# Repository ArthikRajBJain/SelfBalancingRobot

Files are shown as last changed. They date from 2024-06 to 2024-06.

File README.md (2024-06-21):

# Self Balancing Robot

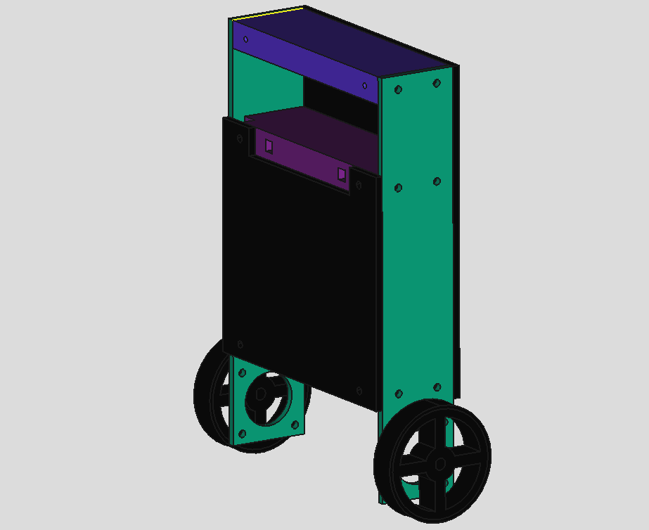
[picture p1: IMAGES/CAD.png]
Watch the video (https://drive.google.com/file/d/1cC-Chdwye79UuMQegcqwbnqvilcww2Fp/view?usp=drive_link)


This is the project involving the development of a Self Balancing Robot. It uses the Proportional, Integraal and Derivative(PID) control algorithm to balance itself. It uses the 6 Degrees of Freedom(DOF) Inertial Measurement Unit(IMU) as the sensor to get the angle data.

<br>
**Process Variable:**  Angle(Roll) (deg)
<br>
**Control Variable:**  Speed of the Motors (mm/sec)
<br>
**Setpoint        :**  0 deg (calibrated for upright position)

<br>

The motors used are the stepper motors hence the relationship between the number of steps and speed is non-linear in nature, hence PID algorithm can not be used unless the linearization is performed.

<br>
$Speed = {157 \over 6400*(40+20n)*10^(-6)}$
Here the speed is calculated in mm/sec, and **n** is the number of steps.
<br>
$n = {(157*10^(6) /over 5400*Speed*20) - (40 /over 20)}$
<br>

To mitigate the problem of nonlinear-system, the PID algoritm is implemented on **Speed** rather than the number of steps **n**.

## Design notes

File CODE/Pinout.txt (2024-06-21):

MotorP
12 - INA
14 - STP
27 - DIR

MotorN
33 - INA
25 - STP
26 - DIR

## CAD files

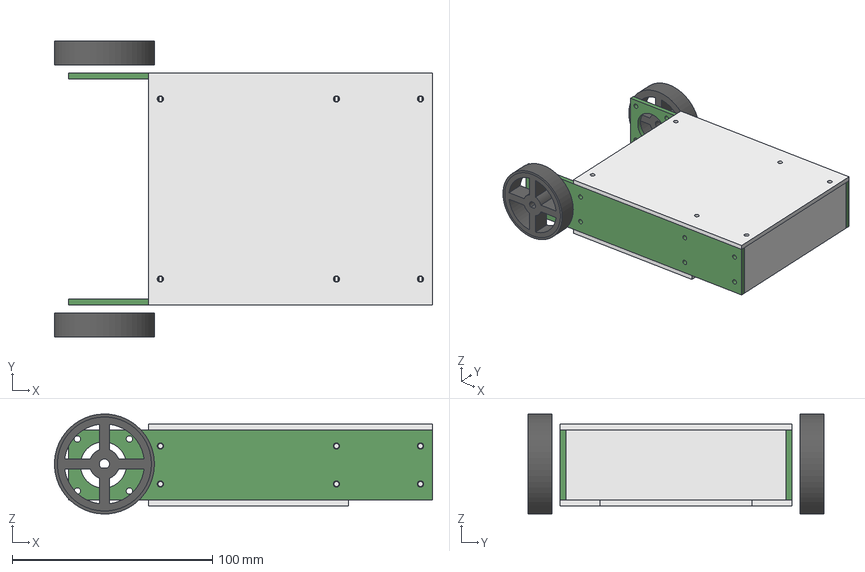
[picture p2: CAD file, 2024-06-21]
CAD/SelfBalancing/SelfBalancing.FCStd
189.0 x 148.0 x 50.0 mm
WheelBody
WheelRubberBody
SideBody
SeparatorBodyTop
SeparatorBodySecond
SeparatorBodyThird
FrontPanelBody
BackPanelBody
WheelBody001
SideBody001
WheelRubberBody001

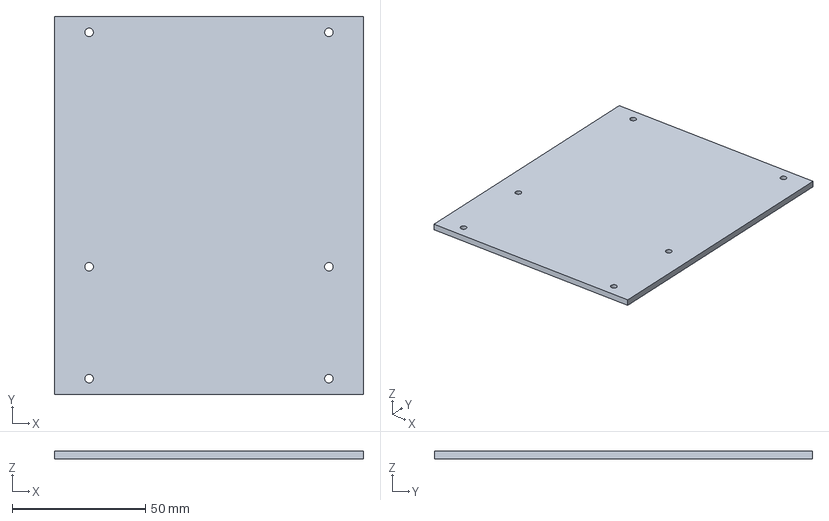
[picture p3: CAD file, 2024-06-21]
CAD/SLICE/SelfBalancing-BackPanelBody.3mf
116.0 x 142.0 x 3.00 mm

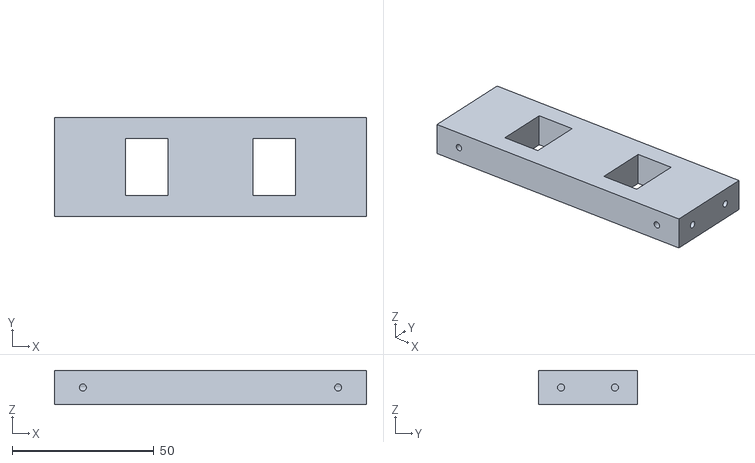
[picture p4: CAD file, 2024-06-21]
CAD/STL/SelfBalancing-SeparatorBodyThird.stl
110.0 x 35.0 x 12.0

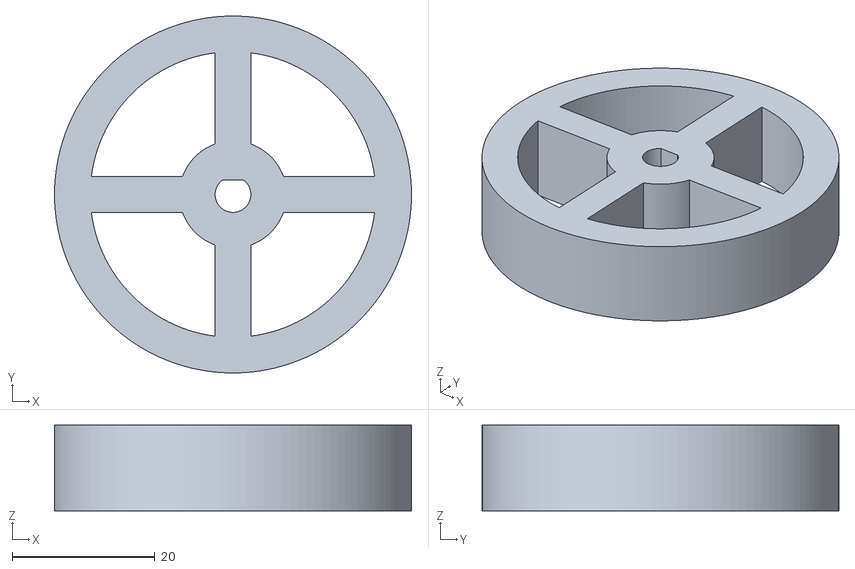
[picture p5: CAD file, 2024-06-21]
CAD/STL/SelfBalancing-WheelBody.stl
50.0 x 50.0 x 12.0

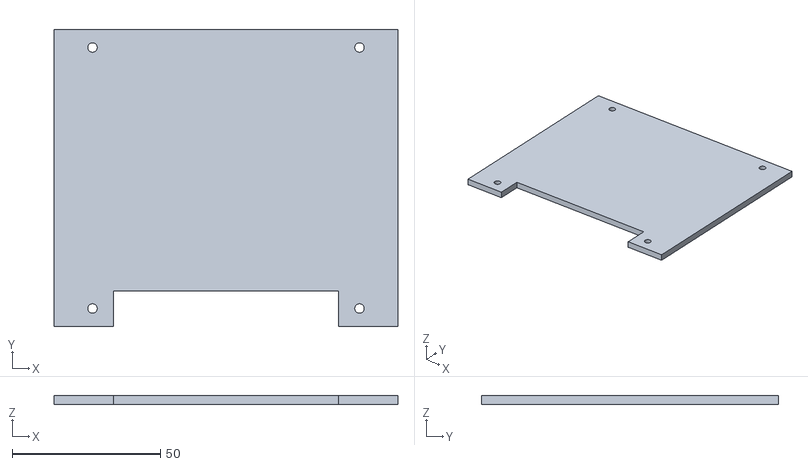
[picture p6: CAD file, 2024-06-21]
CAD/STL/SelfBalancing-FrontPanelBody.stl
116.0 x 100.0 x 3.00

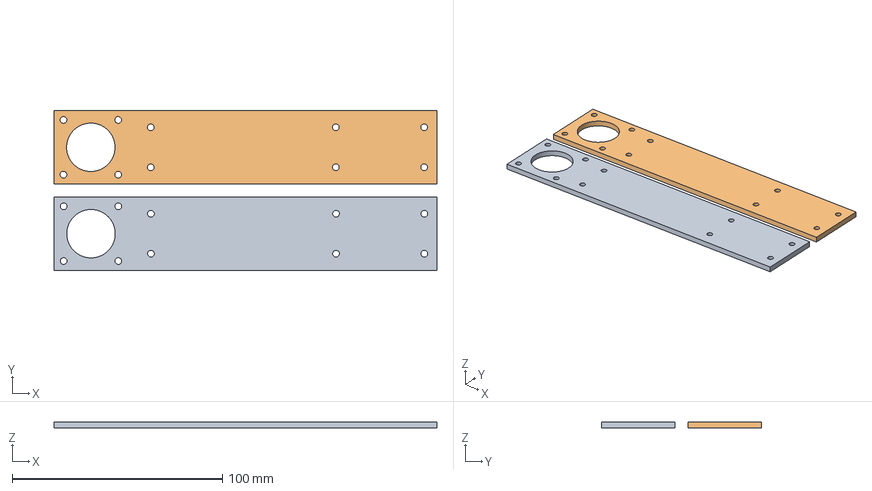
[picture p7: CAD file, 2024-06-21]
CAD/SLICE/SelfBalancing-SideBody.3mf
182.1 x 76.1 x 3.00 mm
SelfBalancing-SideBody.stl x 2

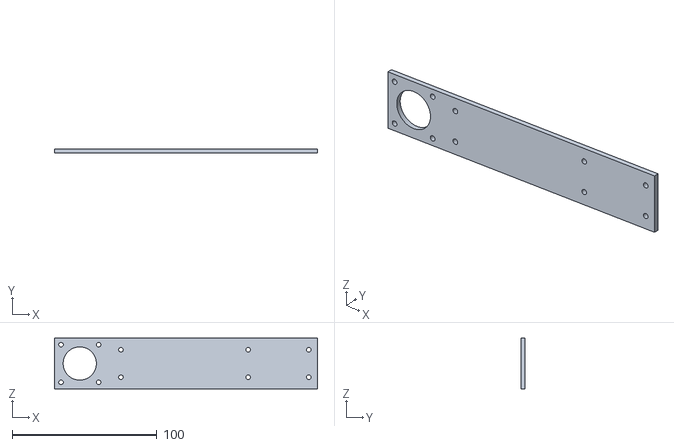
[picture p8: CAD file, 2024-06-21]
CAD/STL/SelfBalancing-SideBody.stl
182.0 x 3.00 x 35.0

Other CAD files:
CAD/SLICE/SelfBalancing-SeparatorBodyTop.3mf
CAD/SLICE/SelfBalancing-SeparatorBodyThird.3mf
CAD/STL/SelfBalancing-SeparatorBodyTop.stl
CAD/SLICE/SelfBalancing-WheelBody.3mf
CAD/STL/SelfBalancing-SeparatorBodySecond.stl
CAD/SLICE/SelfBalancing-FrontPanelBody.3mf
CAD/STL/SelfBalancing-BackPanelBody.stl
CAD/SLICE/SelfBalancing-SeparatorBodySecond.3mf

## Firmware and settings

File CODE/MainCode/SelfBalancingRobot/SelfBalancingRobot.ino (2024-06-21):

#include <WiFi.h>
#include <ESPmDNS.h>
#include <NetworkUdp.h>
#include <ArduinoOTA.h>
#include "BluetoothSerial.h"
#include "Wire.h"
#include "PID.h"
#include "math.h"

const char *ssid = "XXXXXXX";
const char *password = "XXXXXXX";

String device_name = "SelfBalancingRobot";
hw_timer_t *timer = NULL;
double ltime = 0;
double LSpeed = 0, RSpeed = 0, LMotor = 0, RMotor = 0, LMotorCount = 0, RMotorCount = 0;
bool LDirection = 0, RDirection = 0;
bool LITRFlag = 0, RITRFlag = 0;
double input, output, setpoint = 0, Kp = 50, Ki = 0.005, Kd = 0.0001, setpointMem = 0;
bool direction = 0;
int16_t rax, ray, raz, rgx;
double ax, ay, az, axcal, aycal, azcal;
double aroll, groll, grollcal, arollcal;
double froll;

PID pid(&input, &output, &setpoint, Kp, Ki, Kd, direction, micros());

void IRAM_ATTR onTimer() {
  LMotorCount++;
  if (LITRFlag == 1) {
    digitalWrite(25, LOW);
    LITRFlag = 0;
    LMotorCount = 0;
  }
  if (LMotorCount > LMotor) {
    digitalWrite(25, HIGH);
    LITRFlag = 1;
  }

  RMotorCount++;
  if (RITRFlag == 1) {
    digitalWrite(14, LOW);
    RITRFlag = 0;
    RMotorCount = 0;
  }
  if (RMotorCount > RMotor) {
    digitalWrite(14, HIGH);
    RITRFlag = 1;
  }
}

BluetoothSerial SerialBT;

int numFinder(double speed) {
  return int(round((1218.75 / speed) - 2.0));
}

TaskHandle_t task_loop1;
void esploop1(void *pvParameters) {
  setup1();

  for (;;) {
    loop1();
  }
}

void setup() {
  // Motor N
  pinMode(33, OUTPUT);  //INA
  pinMode(25, OUTPUT);  //STP
  pinMode(26, OUTPUT);  //DIR
  // Motor P
  pinMode(12, OUTPUT);  //INA
  pinMode(14, OUTPUT);  //STP
  pinMode(27, OUTPUT);  //DIR
  digitalWrite(33, HIGH);
  digitalWrite(12, HIGH);
  digitalWrite(26, LOW);
  digitalWrite(27, HIGH);
  timer = timerBegin(1000000);
  timerAttachInterrupt(timer, &onTimer);
  timerAlarm(timer, 20, true, 0);
  xTaskCreatePinnedToCore(
    esploop1,               /* Task function. */
    "loop1",                /* name of task. */
    10000,                  /* Stack size of task */
    NULL,                   /* parameter of the task */
    1,                      /* priority of the task */
    &task_loop1,            /* Task handle to keep track of created task */
    !ARDUINO_RUNNING_CORE); /* pin task to core @ */
  Serial.begin(115200);
  ltime = micros() + 4000;
  pid.setOutputLimits(-613, 613);
  pid.updateTime(micros());
  Wire.begin();
  Wire.setClock(400000);
  Serial.begin(115200);
  //POWER MANAGEMENT
  Wire.beginTransmission(0x68);
  Wire.write(0x6B);
  Wire.write(0x00);
  Wire.endTransmission();
  //GYROSCOPE RANGE(+/-250dps)
  Wire.beginTransmission(0x68);
  Wire.write(0x1B);
  Wire.write(0x00);
  Wire.endTransmission();
  //ACCELEROMETER RANGE(+/-4g)
  Wire.beginTransmission(0x68);
  Wire.write(0x1C);
  Wire.write(0x08);
  Wire.endTransmission();
  //FILTERING
  Wire.beginTransmission(0x68);
  Wire.write(0x1A);
  Wire.write(0x03);
  
  Wire.endTransmission();
  ltime = micros();
  for(int i=0;i<500;i++)
  {
    Wire.beginTransmission(0x68);
    Wire.write(0x43);
    Wire.endTransmission();
    Wire.requestFrom(0x68, 2);
    rgx = rgx + Wire.read()<<8|Wire.read();
    while (ltime > micros());
    ltime = micros() + 4000;
  }
  rgx = rgx/500.0;
  grollcal = -rgx*0.000031;
  Wire.beginTransmission(0x68);
  Wire.write(0x3B);
  Wire.endTransmission();
  Wire.requestFrom(0x68, 6);
  rax = Wire.read()<<8|Wire.read();
  ray = Wire.read()<<8|Wire.read();
  raz = Wire.read()<<8|Wire.read();
  ax = rax/8200.0;
  ay = ray/8200.0;
  az = raz/8200.0;
  // arollcal = atan(ax/(sqrt(ay*ay + az*az)))*-57.3;
  arollcal = atan(ay/(sqrt(ax*ax + az*az)))*62.1325;
  pinMode(33, OUTPUT);  //INA
  pinMode(25, OUTPUT);  //STP
  pinMode(26, OUTPUT);  //DIR
  // Motor P
  pinMode(12, OUTPUT);  //INA
  pinMode(14, OUTPUT);  //STP
  pinMode(27, OUTPUT);  //DIR
  digitalWrite(33, LOW);
  digitalWrite(12, LOW);
  digitalWrite(26, LOW);
  digitalWrite(27, HIGH);
  pid.setDeadzone(-5, 5);
}

int number;

void loop() {
  Wire.beginTransmission(0x68);
  Wire.write(0x3B);
  Wire.endTransmission();
  Wire.requestFrom(0x68, 6);
  rax = Wire.read()<<8|Wire.read();
  ray = Wire.read()<<8|Wire.read();
  raz = Wire.read()<<8|Wire.read();
  ax = rax/8192.0;
  ay = ray/8192.0;
  az = raz/8192.0;
  if(az >= 0) aroll = -(arollcal - atan(ay/(sqrt(ax*ax + az*az)))*62.1325);
  else aroll = (arollcal - atan(ay/(sqrt(ax*ax + az*az)))*62.1325);
  Wire.beginTransmission(0x68);
  Wire.write(0x43);
  Wire.endTransmission();
  Wire.requestFrom(0x68, 2);
  rgx = Wire.read()<<8|Wire.read();
  groll = froll + grollcal + rgx*0.000031;
  froll = groll*0.997 + aroll*0.003;

  input = froll;
  pid.compute(micros());
  if((setpointMem == setpoint) && (output != 0))
  {
    if(output > 0)
    {
      setpoint += 0.007;
      setpointMem = setpoint;
    }
    else
    {
      setpoint -= 0.007;
      setpointMem = setpoint;
    }
  }
  if (output >= 0) {
    digitalWrite(26, LOW);
    digitalWrite(27, HIGH);
    number = numFinder(output);
    LMotor = number;
    RMotor = number;
  } else {
    digitalWrite(26, HIGH);
    digitalWrite(27, LOW);
    number = numFinder(-1 * output);
    LMotor = number;
    RMotor = number;
  }

  if(input >  15 || input < -15)
  {
    digitalWrite(33, HIGH);
    digitalWrite(12, HIGH);
  }

  while (ltime > micros());
  ltime = micros() + 4000;
}

void setup1() {
  WiFi.mode(WIFI_STA);
  WiFi.begin(ssid, password);
  SerialBT.begin(device_name);
  while (WiFi.waitForConnectResult() != WL_CONNECTED) {
    SerialBT.println("Connection Failed! Rebooting...");
    delay(5000);
    ESP.restart();
  }
  ArduinoOTA.setHostname("SelfBalancingRobot");
  ArduinoOTA.setPasswordHash("ee338d1db6a6ed2564dc623d8f11bf8b");
  ArduinoOTA
    .onStart([]() {
      String type;
      if (ArduinoOTA.getCommand() == U_FLASH) {
        type = "sketch";
      } else {  // U_SPIFFS
        type = "filesystem";
      }
      SerialBT.println("Start updating " + type);
    })
    .onEnd([]() {
      SerialBT.println("\nEnd");
    })
    .onProgress([](unsigned int progress, unsigned int total) {
      SerialBT.printf("Progress: %u%%\r", (progress / (total / 100)));
    })
    .onError([](ota_error_t error) {
      SerialBT.printf("Error[%u]: ", error);
      if (error == OTA_AUTH_ERROR) {
        SerialBT.println("Auth Failed");
      } else if (error == OTA_BEGIN_ERROR) {
        SerialBT.println("Begin Failed");
      } else if (error == OTA_CONNECT_ERROR) {
        SerialBT.println("Connect Failed");
      } else if (error == OTA_RECEIVE_ERROR) {
        SerialBT.println("Receive Failed");
      } else if (error == OTA_END_ERROR) {
        SerialBT.println("End Failed");
      }
    });
  ArduinoOTA.begin();
}

char byt;
double KpBT = 0, KiBT = 0, KdBT = 0;
String val;
double remoteTime = 0;

void loop1() {
  ArduinoOTA.handle();
  if(SerialBT.available()) {
    byt = SerialBT.read();
    if(byt == 'P') {
      val = SerialBT.readStringUntil(' ');
      KpBT = val.toDouble();
    }
    if(byt == 'I') {
      val = SerialBT.readStringUntil(' ');
      KiBT = val.toDouble();
    }
    if(byt == 'D') {
      val = SerialBT.readStringUntil('\n');
      KdBT = val.toDouble();
      pid.setTunings(KpBT, KiBT, KdBT);
      SerialBT.print(KpBT);
      SerialBT.print(" ");
      SerialBT.print(KiBT);
      SerialBT.print(" ");
      SerialBT.println(KdBT);
    }
    if(byt == 'F')
    {
      setpoint += 0.7;
    }
    if(byt == 'B')
    {
      setpoint += -0.7;
    }
    if(byt == 'S')
    {
      setpoint = setpointMem;
    }
  }
  SerialBT.print(input);
  SerialBT.print(" ");
  SerialBT.print(setpoint);
  SerialBT.print(" ");
  SerialBT.println(output);
  // Serial.print(input);
  // Serial.print(" ");
  // Serial.print(setpoint);
  // Serial.print(" ");
  // Serial.println(output);
  vTaskDelay(1);
}

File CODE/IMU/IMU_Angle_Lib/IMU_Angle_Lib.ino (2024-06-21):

#include "Wire.h"


int16_t rax, ray, raz, rgx, rgy, rgz;
double ax, ay, az, axcal, aycal, azcal;
double vector;
double ayaw, apitch, aroll, gyaw, gpitch, groll, gyawcal, gpitchcal, grollcal, ayawcal, apitchcal, arollcal;
double fyaw, fpitch, froll;
double ltime;

void setup() 
{
  Wire.begin();
  Wire.setClock(400000);
  Serial.begin(115200);
  //POWER MANAGEMENT
  Wire.beginTransmission(0x68);
  Wire.write(0x6B);
  Wire.write(0x00);
  Wire.endTransmission();
  //GYROSCOPE RANGE(+/-250dps)
  Wire.beginTransmission(0x68);
  Wire.write(0x1B);
  Wire.write(0x00);
  Wire.endTransmission();
  //ACCELEROMETER RANGE(+/-4g)
  Wire.beginTransmission(0x68);
  Wire.write(0x1C);
  Wire.write(0x08);
  Wire.endTransmission();
  //FILTERING
  Wire.beginTransmission(0x68);
  Wire.write(0x1A);
  Wire.write(0x03);
  Wire.endTransmission();
  ltime = micros();
  for(int i=0;i<500;i++)
  {
    Wire.beginTransmission(0x68);
    Wire.write(0x43);
    Wire.endTransmission();
    Wire.requestFrom(0x68, 6);
    rgx = rgx + Wire.read()<<8|Wire.read();
    rgy = rgy + Wire.read()<<8|Wire.read();
    rgz = rgz + Wire.read()<<8|Wire.read();
    while (ltime > micros());
    ltime = micros() + 4000;
  }
  rgx = rgx/500.0;
  rgy = rgy/500.0;
  rgz = rgz/500.0;
  grollcal = -rgx*0.000031;
  gpitchcal = -rgy*0.000031;
  gyawcal = -rgz*0.000031;
  Wire.beginTransmission(0x68);
  Wire.write(0x3B);
  Wire.endTransmission();
  Wire.requestFrom(0x68, 6);
  rax = Wire.read()<<8|Wire.read();
  ray = Wire.read()<<8|Wire.read();
  raz = Wire.read()<<8|Wire.read();
  ax = rax/8200.0;
  ay = ray/8200.0;
  az = raz/8200.0;
  apitchcal = atan(ay/(sqrt(ax*ax + az*az)))*-57.3;
  arollcal = atan(ax/(sqrt(ay*ay + az*az)))*-57.3;
}

double start;

void loop() 
{
  start = micros();
  Wire.beginTransmission(0x68);
  Wire.write(0x3B);
  Wire.endTransmission();
  Wire.requestFrom(0x68, 6);
  rax = Wire.read()<<8|Wire.read();
  ray = Wire.read()<<8|Wire.read();
  raz = Wire.read()<<8|Wire.read();
  ax = rax/8200.0;
  ay = ray/8200.0;
  az = raz/8200.0;
  apitch = apitchcal + atan(ay/(sqrt(ax*ax + az*az)))*57.3;
  aroll = arollcal + atan(ax/(sqrt(ay*ay + az*az)))*57.3;
  Wire.beginTransmission(0x68);
  Wire.write(0x43);
  Wire.endTransmission();
  Wire.requestFrom(0x68, 6);
  rgx = Wire.read()<<8|Wire.read();
  rgy = Wire.read()<<8|Wire.read();
  rgz = Wire.read()<<8|Wire.read();
  groll = froll + grollcal + rgx*0.000031;
  gpitch = fpitch + gpitchcal + rgy*0.000031;
  gyaw = gyaw + gyawcal + rgz*0.000031;
  fyaw = gyaw;
  fpitch = gpitch*0.9995 + apitch*0.0005;
  froll = groll*0.9995 + aroll*0.0005;
  // vector = sqrt(ax*ax + ay*ay + az*az);
  // ayaw = acos(ax/vector)*57.2956;
  // apitch = acos(ay/vector)*57.2956;
  // aroll = acos(az/vector)*57.2956;
  // Serial.print(micros()-start);
  // Serial.print(" ");
  // Serial.print(groll);
  // Serial.print(" ");
  // Serial.print(gpitch);
  // Serial.print(" ");
  // Serial.println(gyaw);
  // Serial.print(micros()-start);
  // Serial.print(" ");
  // Serial.print(ayaw);
  // Serial.print(" ");
  // Serial.print(apitch);
  // Serial.print(" ");
  // Serial.println(aroll);
  Serial.print(micros()-start);
  Serial.print(" ");
  Serial.print(fyaw);
  Serial.print(" ");
  Serial.print(fpitch);
  Serial.print(" ");
  Serial.println(froll);
  while (ltime > micros());
  ltime = micros() + 4000;
}

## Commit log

2024-06-21 Self Balancing Robot working
    [SelfBalancing-BackPanelBody.3mf, SelfBalancing-BackPanelBody.stl, SelfBalancing-FrontPanelBody.3mf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]
2024-06-21 Updated CAD
    [SelfBalancing-BackPanelBody.3mf, SelfBalancing-BackPanelBody.stl, SelfBalancing-FrontPanelBody.3mf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]
